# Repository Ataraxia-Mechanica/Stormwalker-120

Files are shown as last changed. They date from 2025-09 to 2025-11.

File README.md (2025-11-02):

# Stormwalker 120

Discord server:

https://discord.gg/DXYpTaRm

Stormwalker 120 is a Voron 0 sized (120mm^3 build size), ultra fast 3D printer designed for rapid prototyping. Press and forget, go through iterations in minutes!

in enclosure
nobackdrop-2k

# Project Currently Under Construction

Progress is currently made towards an assembly manual covering how to build and tune this printer, though it's possible to build it from just the BOM and referencing the 3D model in Blender.

If sourcing the components are hard or expensive, please wait for the kit of this printer as I am determined to make it a reality.

# Input Shaper Graph
x_new
y

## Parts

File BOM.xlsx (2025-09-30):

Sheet: Body
Category | Component/Item | Variant | Qty | Notes
Filament
Filament | ABS-GF | Fusrock NexABS-GF25 (Coextrusion 25% fill) 1kg | 1 | Qidi also sells repackaged fusrock. Non-coextruded ABS-GF would work.
Filament | PET-GF | FusRock FusForce PET-GF 500g | 1 | PET-CF would work. DO NOT BUY FROM POLYMAKER/BAMBU, FAILS DURING ANNEALING
Filament | MATTE PETG | 1kg | 1 | For Ebox, helper tools and fan duct.
Frame
Aluminum Extrusion | 3060 extrusion (3mm thickness) (Custom ordered) | 225mm | 2 | Commonly found 2mm thickness ones would work at reduced performance. Check custom ordered parts folder for holes/tapping
Aluminum Extrusion | 3060 extrusion (3mm thickness) (Custom ordered) | 200mm | 1
Aluminum Extrusion | 3060 extrusion (3mm thickness) (Custom ordered) | 140mm | 1
Steel Plate | Steel Plate (Custom ordered) | 304 stainless steel, 8mm thickness | 1 | 215mm*215mm*8mm
Frame Bracket | 90 Degree 3030 Corner Bracket |  | 2 | Optional. Check model for clearance. Some variants would limit max Z travel.
Rubber Feet | 40mm Screw Mount Round Large Rubber Feet | M6 hole | 4
Motion
Belt | Gates EPDM LL-2GT-9mm High Temperature Belt | 2.4mm closed loop belt | 1 | Uses ~800mm for Y axis and ~550mm for X.
Pulleys | Gates 2GT 20 tooth pulley | 8mm bore, 9mm wide | 4 | Use geniue Gates/Runice high matching pulleys. Do not cheap out. 9mm and 10mm wide pulleys are the same thing (11mm groove width).
Pulleys | Gates 2GT 20 tooth pulley | 5mm bore, 9mm wide | 2
Bearing | Bearing 625ZZ | ABEC7/P4 | 2 | ABEC 5/P5 min, ABEC7/P4 or better recommended.
Stepper Motor | Moons' NEMA17 2A | MS17HD6P420I-04 | 2
Stepper Motor | SUMTOR 1.3A NEMA17 8mm shaft | 42HS813A4D8 | 4
Stepper Motor | Integrated Lead Screw Stepper | Nema17 40mm TR8x1 | 2 | Commonly found TR8x2 would work, but 1mm thread pitch helps with layer stacking quality.
Heatsink | Heatsink | 30x40x5mm | 14 | 3 of each for X steppers, and 2 of each for Y steppers
Toolhead
Stepper Motor | Moon's Nema14 Pancake 10T | CSE14RA1L410A-01 | 1 | Must be 10T.
Extruder | K1 all metal extruder gear | Double bearing | 1 | Comes in pairs, only need one. Must be double bearing variant, see image on the right.
Extruder | K1 all metal reduction gear |  | 1
Hotend | TZ-E3 2.0 |  | 1
Hotend Extender | 35mm Super Extender (Custom ordered) |  | 1 | Check custom ordered parts folder. Might need to screw in a M6 screw for a few times to loosen it due to thin walls and bad manufacturing.
Belt Clip | X Axis Belt Clip (Custom ordered) |  | 2
Thermistor | Generic 3950 Thermistor | glass bead, 1.2mm diameter | 1
Heater | Ceramic Heater 7mm*35mm | 7~8Ω | 1
Bearing | Miniature Bearing MR63ZZ | ABEC7/P4 | 1 | ABEC7/P4 or better recommended. Replaces the low quality one from K1 reduction gear.
Bearing | Miniature Bearing 693ZZ | ABEC7/P4 | 1 | ABEC7/P4 or better recommended. Add to the front of the extruder gear for extra stability.
Bearing | U Groove Bearing U624ZZ | 1.5mm wide*0.5mm deep groove | 1
PTFE Tube | PTFE Tube | 1.8mm ID * 2.6mm OD | 1 | Smaller diameter tubes constrain the filament better.
Pin | Stainless Steel Pin | 3mm*14mm | 1
Pin | Stainless Steel Pin | 3mm*20mm | 1
Pin | Stainless Steel Pin | 4mm*10mm | 1
Hotend Cooling Fan | 3015 Fan | 24V 12000RPM | 1 | Higher the CFM the better. At least 5CFM.
Spring | Sherpa Mini Spring | 0.7mm Wire Width*5mm OD*15mm Length | 1
Bimetal Nozzle | Bimetal Volcano Nozzle |  | 1
Rail
Linear Rail | MGW15 | 200mm (Z1 preload) | 1 | Cheap ones work just as well.
Linear Rail | MGW9 | 240mm (Z1 preload), 2 carriages | 2
Linear Rail | Airtac LRW9L | LRW9L 1X174S12AH | 2 | Must be Airtac and no preload.
Bed
Carbon Fiber Bed | Carbon Fiber Sheet (Custom ordered) | 120*120mm (3K - 4mm Plain Matte) | 1 | Check custom ordered parts folder.
Heater | 1mm Aluminum PCB (Custom ordered) |  | 1
Thermister | Generic 3950 100K | Surface Mounted 0805 Size | 1
Magnetic Sheet | 2mm Magnetic Sheet | Extra strong, 120mm*120mm | 1 | Optional.
PEI Sheet | Voron 0 Textured PEI |  | 1 | Consider getting 2 of them to minimize downtime between prints.
Cooling
Cooling Fan | Delta 4056 Fan | GFC0412DS-SM06 | 3 | Weaker variants would work.
Misc.
Popcorn Salt | Popcorn Salt |  | 200g | Pack PET parts tightly in salt and air fry for 2 hours at 130-140C.
Glue | 425 Glue |  | 1 | Basically plastic-safe threadlocker. Apply on screws after installing. Warning: if accidentally went into screw socket, immediately insert screwdriver into socket and wait 30 seconds for it to dry to prevent gluing the socket shut.
Glue | 407 Glue |  | 1
RTV Silicone | RTV Silicone | Temp resistant to 300℃ | 1
Dish Soap | Dish Soap |  | 5mL | For making custom RTV silicone socks. Rinse the mold with dish soap water.
Lubrication Grease | Mobilux EP2 |  | 5mL | For lubricating linear rails.
Lubrication Grease | PTFE Grease |  | 5mL | For lubricating lead screws and extruder gears.
Thermal Paste | Thermal Paste | Temp resistant to 350℃ | 2mL | Paste eaters are the most oppressed group in society. Replaces the godawful GD900 that comes with TZE3.

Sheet: Ebox&Wiring
Category | Component/Item | Variant | Qty | Notes
Electronics
Power Supply | LRS-350-24 |  | 1
Power Supply | LRS-150-48 |  | 1
Board | Fly-C8 |  | 1
WiFi Dongle | WiFi Dongle | MT7601 | 1 | Fly-C8 doesn't support the addon WiFi module if you don't use the bloat filled system image. Flawless design.
SD Card | SD Card | 32GB | 1
Stepper Driver | Stepper Driver | TMC2209 | 2 | Z axis.
Stepper Driver | Stepper Driver | TMC2240 | 1 | E axis.
Stepper Driver | Stepper Driver | TMC5160 | 2
MOSFET Board | MOSFET Board | 10A peak | 1 | The board's default fan ports can't keep up with 2.8A server fans.
Breakout Board
Breakout Board | Microbreak board (Custom ordered) |  | 1 | Check custom ordered parts folder.
Wire Connector | Micro-Fit 3.0 Vertical Header, Dual Row | 430452412 (2x12) | 1
Wire Connector | Micro-Fit 3.0 Vertical Header, Dual Row | 430452012 (2x10) | 1
Wire Connector | JST XH Series Straight Through Hole PCB Header | 2 Pin | 12
Wire Connector | JST XH Series Straight Through Hole PCB Header | 4 Pin | 9
Screw Terminal Block | Screw Terminal Block | 2pin, 3.5mm pitch | 3 | Both top entry and side entry would work.
Harness
Crimp Terminal | Micro-Fit 3.0 Crimp Terminal, Female |  | 50 | Uses 43. Buy extra if not confident with wiring.
Wire | Insulated wire | 26AWG | 15m
Wire | Insulated wire | 20AWG | 15m
Wire Housing | Micro-Fit 3.0 Receptacle Housing, Dual Row | 430252400 (2x12) | 1 | Buy extra if not confident with wiring.
Wire Housing | Micro-Fit 3.0 Receptacle Housing, Dual Row | 430252000 (2x10) | 1
Wire Connector | JST XH Series Connector | 2 Pin | 12
Wire Connector | JST XH Series Connector | 4 Pin | 9
Wiring
Wire Connector | JST XH Series Connector | 2 Pin | 12
Wire Connector | JST XH Series Connector | 3 Pin | 4
Wire | Silicone wire | 26AWG | 5m | For wiring thermistors and endstops.
Wire | Silicone wire | 20AWG | 8m | For wiring heaters and fans.
Wire | Silicone wire | 16AWG, Black | 1m | Neutral/-
Wire | Silicone wire | 16AWG, Red | 1m | Live/24V
Wire | Silicone wire | 16AWG, Green+Yellow | 1m | GND
Wire | Silicone wire 4 Strand | 20AWG | 230mm | For bed heater and thermistor.
Wire Splicing Connector | Wago 221-413 |  | 4
Misc.
Endstops | D2F style microswitch | No lever | 4 | Use expensive ones for Z axis. Can use cheap ones for X and Y.
Wire Sleeve | Split Braided Sleeving | 6mm | 2m | 600mm for toolhead and 1.2m for harness.
Ebox Cooling Fan | Fan | 9225 | 2
Power Socket | AC-17 IEC320 C14 Electrical AC Power Socket | With top and bottom screw holes | 1

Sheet: Fasteners
Category | Component/Item | Variant | Qty | Notes
Screws (Body)
Screw | Self Tapping | M2x10 | 4 | For X and Y endstops.
Screw | BHCS | M2x35 | 2
Screw | BHCS | M3x6 | 4
Screw | BHCS | M3x10 | 4
Screw | BHCS | M3x14 | 5
Screw | BHCS | M3x20 | 4
Screw | BHCS | M6x12 | 12 | 4 extra for Y belt tensioner.
Screw | BHCS | M6x30 | 8
Screw | BHCS | M6x50 | 2
Screw | BHCS | M8x35 | 6
Screw | BHCS | M8x90 | 2
Screw | Small Head Screw | M3x16, head diameter 4.5mm | 2 | Oops. Doesn't have enough clearance for regular screws on the toolhead unless you switch to LDO pancake motor and lose torque.
Screw | Ultra Low Head Socket Cap | M4x14 | 4 | Lower than 1.2mm head height, so it can sink below the magnetic sheet.
Screw | SHCS | M1.6x12 TC4 | 4 | Must be in titanium TC4 for hotend double shear.
Screw | SHCS | M3x8 | 4
Screw | SHCS | M3x10 | 29
Screw | SHCS | M3x12 | 29
Screw | SHCS | M3x22 | 8
Screw | SHCS | M3x25 | 12
Screw | SHCS | M3x30 | 8
Screw | SHCS | M3x35 | 4
Screw | SHCS | M3x50 | 2
Screw | SHCS | M3x60 | 12
Screw | SHCS | M4x16 | 10
Screw | SHCS | M5x30 | 8
Screws (Ebox)
Screw | FHCS | M4x8 | 4
Screw | FHCS | M3x10 | 4
Screw | SHCS | M3x35 | 8
Screw | BHCS | M3x6 | 18
Nuts
Nut | M3 Nut |  | 2
Nut | M4 Nut |  | 10
Nut | M6 Nut |  | 12
Self-Clinching Nut | Self-Clinching Nut | CLS-M6-00 (304 stainless steel, thinnest variant) | 1 | For hotend double shear. Stainless steel ones are preferred due to low heat conduction.
T nut | 2020 M3 Nut |  | 32 | Due to the geometry of the 3.0mm 3060 extrusion, only 2020 nuts can fit in. Use NoDrop nuts provided to hold them in place during assembly. If using normal 3060 extrusion, get 3030 ones.
T nut | 2020 M5 Nut |  | 8
Threaded Heat Insert | M1.6 Threaded Heat Insert | M1.6x2.5x5 | 4 | Dimensions are in hole diameter x outer diameter x height. Some vendors use hole diameter x height x outer diameter, check before buying.
Threaded Heat Insert | M2 Threaded Heat Insert | M2x3x4 | 2
Threaded Heat Insert | M3 Threaded Heat Insert | M3x5x4 ("Voron Style") | 44
Threaded Heat Insert | M3 Threaded Heat Insert | M3x5x10 | 12
Threaded Heat Insert | M6 Threaded Heat Insert | M6x8x10 | 6 | 4 of them are for belt tensioner.
Shim
Shim | M3 Shim | M3x16x1, stainless steel | 2 | 10mm~16mm diameter ones would work. Grind the top surface on the extrusion away, and put the sharp side of the shim towards the extrusion to ground the frame.

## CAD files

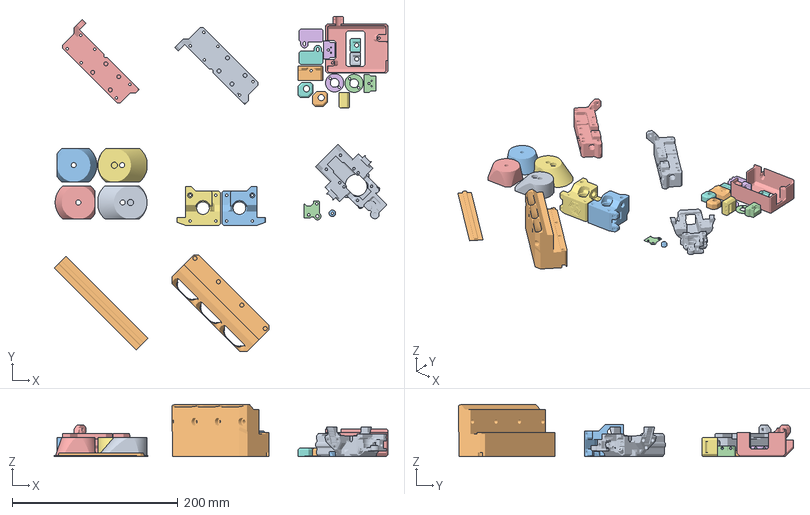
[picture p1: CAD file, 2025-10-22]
3mf/ABS-GF.3mf
402.6 x 404.4 x 62.8 mm
Longboi_toolhead.stl
Aux_Cooling.stl
TZE3_plug.stl
Front_cover.stl
PCB_cover.stl
PCB_spacer_A.stl
Slim_Feet_Support_Back.stl x 2
PCB_spacer_B.stl
Toolhead_Strain_Relief.stl
Slim_Feet_Support_Front.stl x 2
Nut_Shim.stl x 2
Motor_Mount.stl
Feet_Holder.stl x 2
Long_Z.stl x 2
Motor_Mount_Left.stl
Z_Endstop.stl x 2
Y_endstop.stl
NoDrop-2020_chopped.stl x 2
3030_cover.stl

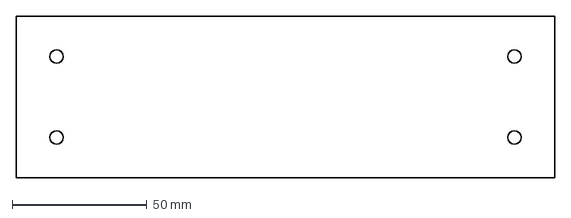
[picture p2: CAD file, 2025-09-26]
custom ordered parts/3060 extrusions/Extrusion Holes.dxf
200.0 x 60.0 mm

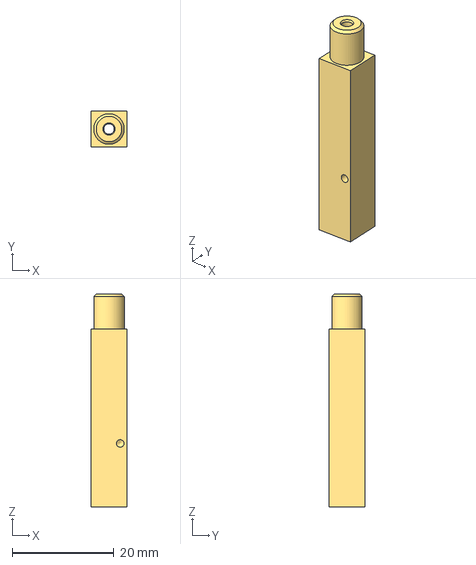
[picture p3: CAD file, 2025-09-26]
custom ordered parts/35mm super extender/Super Extender 35mm.step
7.00 x 7.00 x 41.9 mm

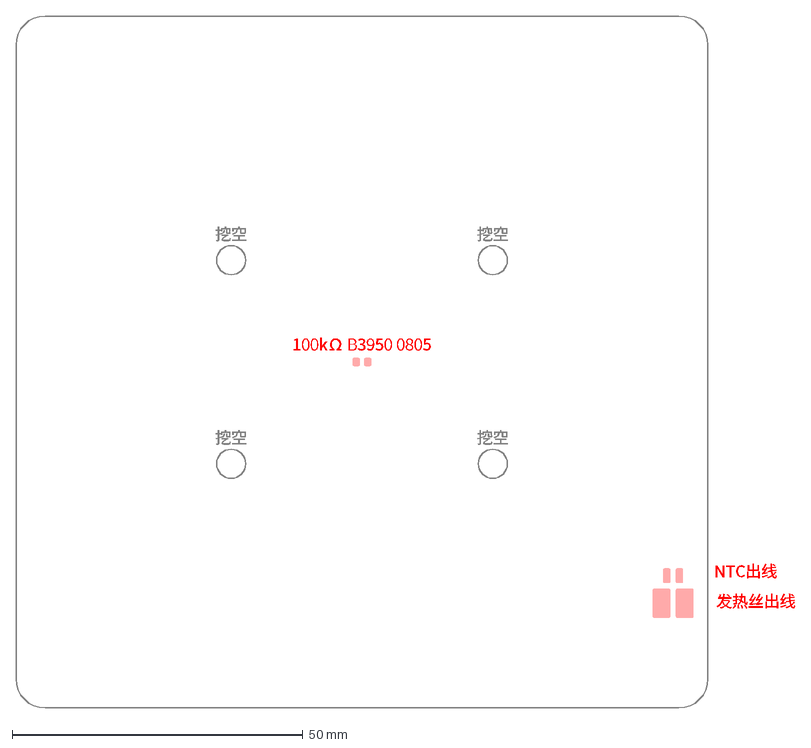
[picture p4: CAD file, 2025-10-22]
custom ordered parts/custom_PI_heater/24V 125W.dxf
100kΩ B3950 0805
NTC出线
发热丝出线
挖空

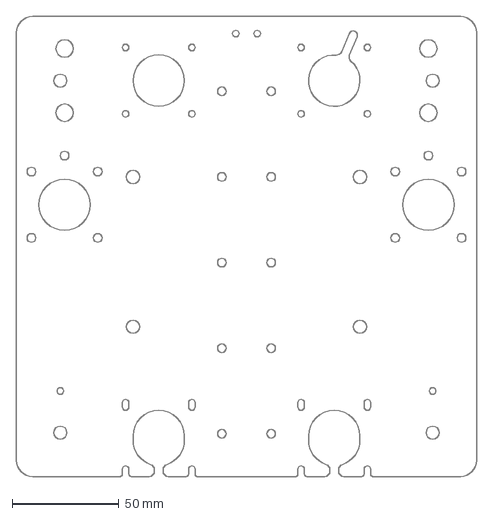
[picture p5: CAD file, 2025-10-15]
custom ordered parts/Steel bottom plate 8mm.dxf
215.0 x 215.0 mm

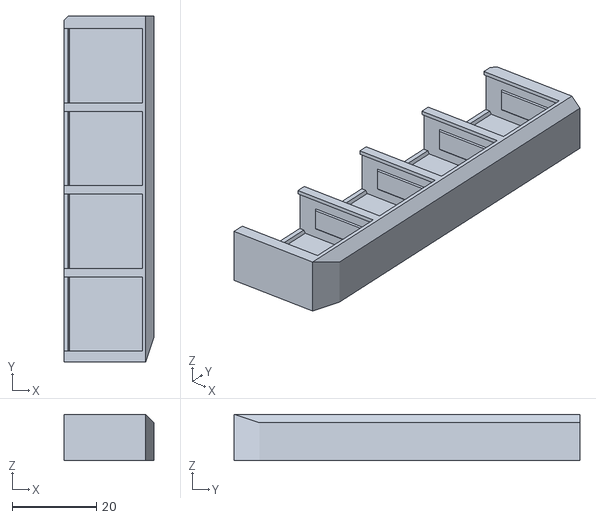
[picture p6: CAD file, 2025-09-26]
micro ebox/stl/4x_Wago_221.stl
21.4 x 82.0 x 11.0

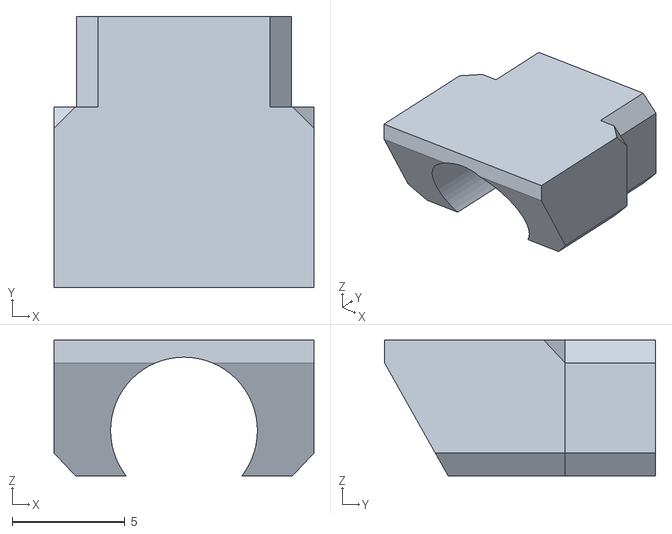
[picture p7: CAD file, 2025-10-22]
stl/Bed_Strain_Relief.stl
11.5 x 12.0 x 6.00

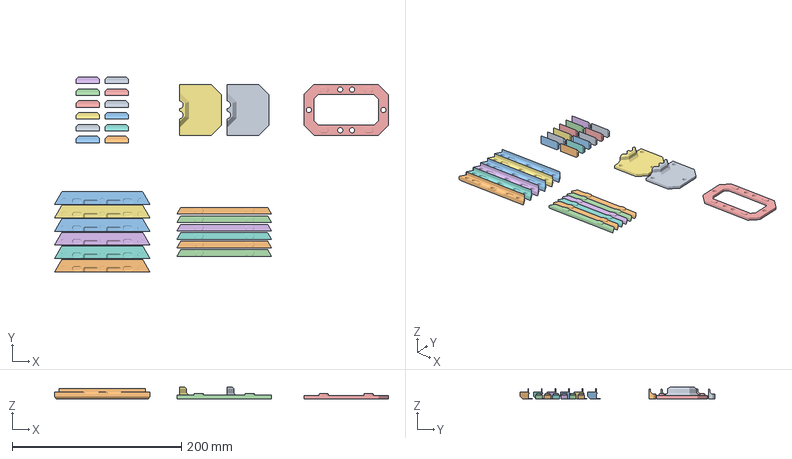
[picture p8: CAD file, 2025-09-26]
storm-in-a-box/3mf/Magnetic_Attacher.3mf
394.4 x 230.5 x 14.0 mm
Magnetic_Attacher.stl x 12
Panel_Attacher.stl x 6
Panel_Support.stl x 6
Ring.stl
Cover.stl x 2

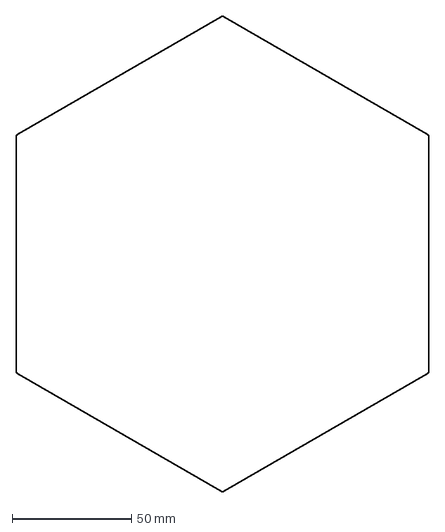
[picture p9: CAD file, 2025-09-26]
storm-in-a-box/Acrylic (5mm).dxf
173.2 x 199.8 mm

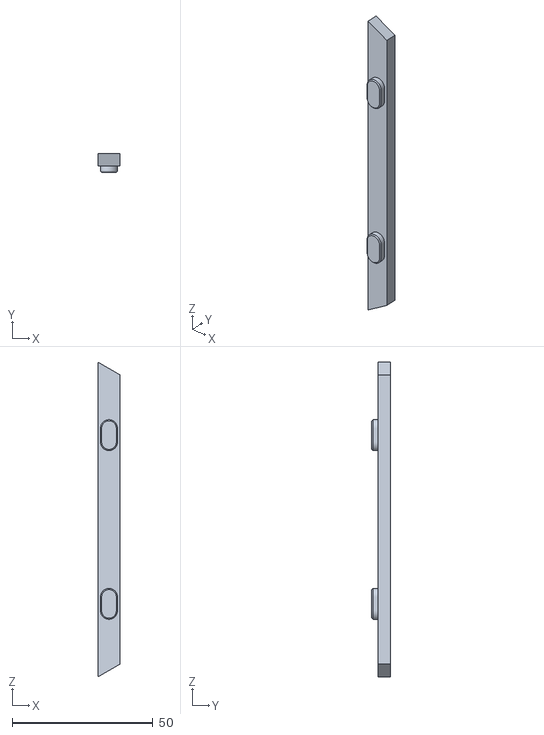
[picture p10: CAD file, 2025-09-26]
storm-in-a-box/stl/Panel_Attacher.stl
8.00 x 6.60 x 112.0

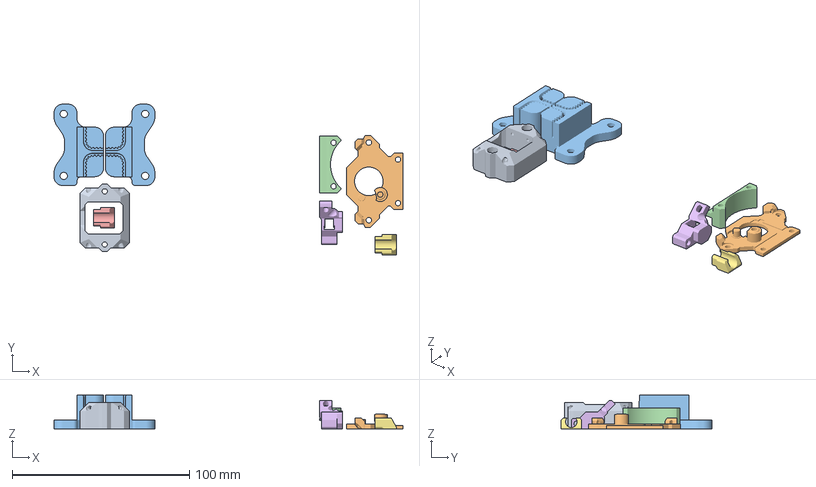
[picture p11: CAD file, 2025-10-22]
3mf/PET.3mf
197.1 x 85.1 x 19.0 mm
Crossover_Toolhead_PET.stl
Extruder_back_panel.stl
Assembly
Extruder_motor_support.stl
Bed_Strain_Relief.stl x 2
Idler_arm.stl

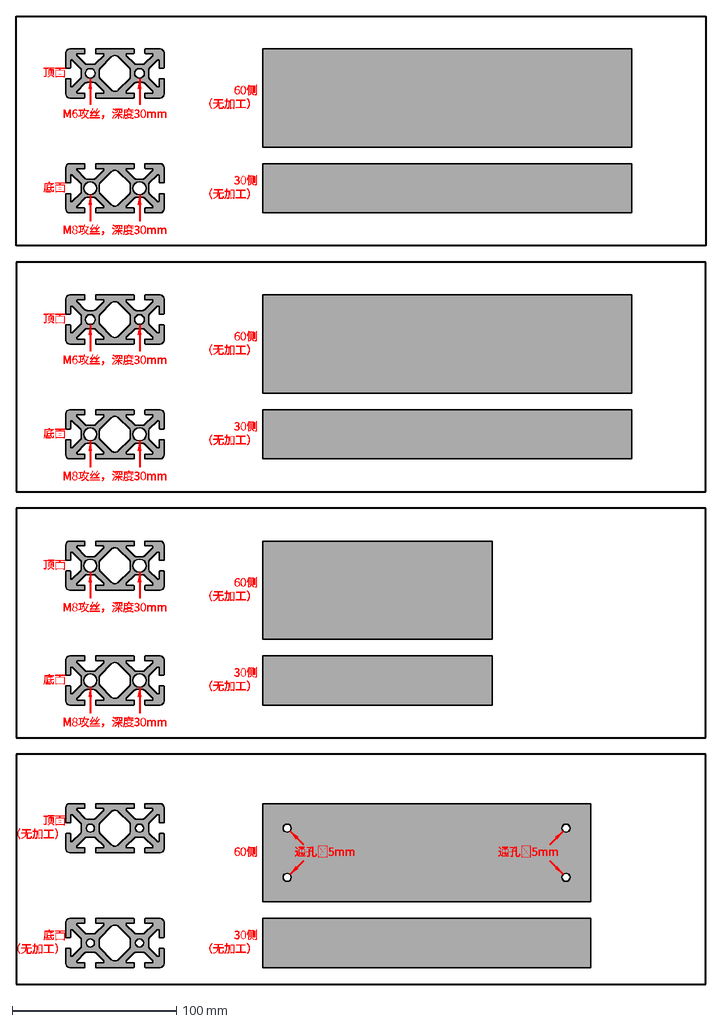
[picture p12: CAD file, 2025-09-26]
custom ordered parts/3060 extrusions/Extrusions.dxf
顶面
底面
60侧 （无加工）
30侧 （无加工）
顶面 （无加工）
底面 （无加工）
60侧
M8攻丝，深度30mm
M6攻丝，深度30mm

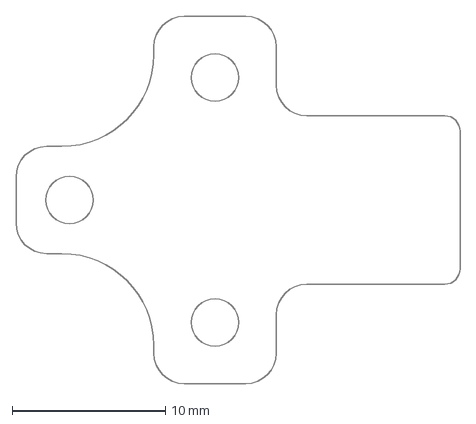
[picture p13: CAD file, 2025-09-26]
custom ordered parts/6061 X clip 3mm.dxf
29.0 x 24.0 mm

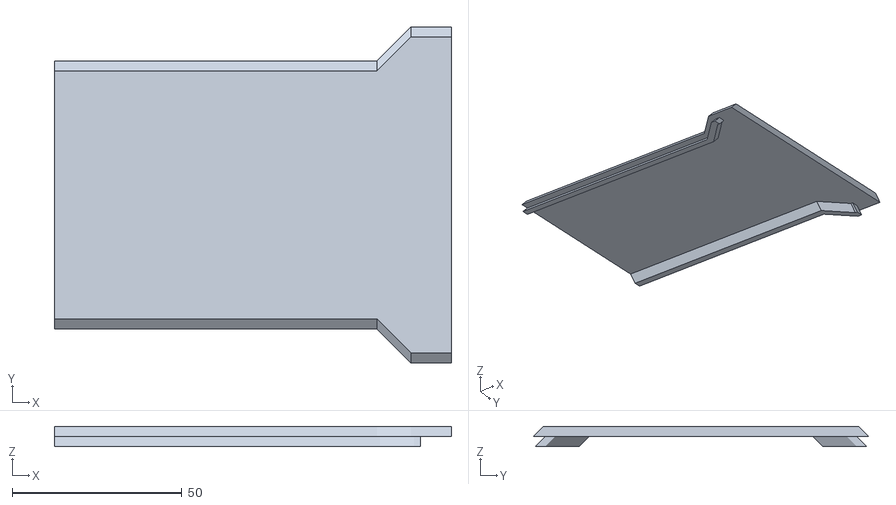
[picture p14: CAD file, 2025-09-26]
micro ebox/stl/Shell3.stl
117.0 x 99.0 x 6.00

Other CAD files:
stl/Extruder_back_panel.stl
storm-in-a-box/3mf/Light.3mf
storm-in-a-box/stl/Light2.stl
3mf/Sock.3mf
3mf/Extra_Ballast.3mf
3mf/PETG.3mf
Jigs & Tools.blend
custom ordered parts/35mm super extender/Super Extender 35mm.dxf
custom ordered parts/CF bed 4mm.dxf
micro ebox/stl/Back.stl
micro ebox/stl/Front.stl
micro ebox/stl/Shell1.stl
micro ebox/stl/Shell2.stl
micro ebox/stl/Shell4.stl
micro ebox/stl/Shell5.stl
micro ebox/stl/Shell6.stl
micro ebox/stl/Wedge.stl
micro ebox/stl/Wire_out.stl
micro ebox/stl/ebox.3mf
stl/3030_cover.stl
stl/Bed_Support.stl
stl/Crossover_Toolhead.stl
stl/Crossover_Toolhead_ABS.stl
stl/Crossover_Toolhead_PET.stl
stl/Extra_Ballast.stl
stl/Extruder_motor_support.stl
stl/Extruder_motor_support_COMPROMISE.stl
stl/Feet_Holder.stl
stl/Front_cover.stl
stl/Idler_arm.stl
stl/Long_Z.stl
stl/Motor_Mount.stl
stl/Motor_Mount_Left.stl
stl/NoDrop-2020.stl
stl/NoDrop-2020_chopped.stl
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

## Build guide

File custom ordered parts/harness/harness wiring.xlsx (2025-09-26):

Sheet: 24pin
name | type | wire gauge | pin
EM1 | XHP4 | 22 | 14 |  | motor slot 8
 |  |  | 13
 |  |  | 2
 |  |  | 1
XR0 | SCREW TERMINAL | 22 | 3 | + | PD13
 |  |  | 4 | -
XR1 | SCREW TERMINAL | 22 | 5 | + | PD14
 |  |  | 6 | -
XEND1 | XHP3 | / | / |  | PD10
 |  | / | /
 |  | 26 | 7
XM | SCREW TERMINAL | 22 | 8 | A+ | TMC5160X | cooling fan: PA1
 |  |  | 9 | A-
 |  |  | 10 | B+
 |  |  | 11 | B-
AUXF | SOLDERING | 22 | 12 | - | PD12 (through mosfet) | mosfet fan: PA2
 |  |  | 24 | +
HEF | XHP2 | 26 | 15 |  | PC7
 |  |  | 16
XTH0 | XHP2 | 26 | 17 |  | PC4
 |  |  | 18
XTH1 | XHP2 | 26 | 19 |  | PC3
 |  |  | 20
GND | SCREW TERMINAL | 22 | 21 | GND
FANPWM | XHP2 | / | / |  | PC6
 |  | 26 | 23

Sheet: 20pin
name | type | wire gauge | pin
YR1 | SCREW TERMINAL | 22 | 1 | + | PB0
 |  |  | 2 | -
YTH1 | XHP2 | 26 | 3 |  | PC2
 |  |  | 4
ZM0 | XHP4 | 26 | 15 |  | motor slot 6
 |  |  | 16
 |  |  | 6
 |  |  | 5
YM | SCREW TERMINAL | 22 | 7 | A+ | TMC5160Y | cooling fan: PA0
 |  |  | 8 | A-
 |  |  | 9 | B+
 |  |  | 10 | B-
ZEND0 | XHP3 | / | / |  | PD8
 |  | / | /
 |  | 26 | 11
ZEND1 | XHP3 | / | / |  | PD9
 |  | / | /
 |  | 26 | 12
YEND1 | XHP3 | / | / |  | PD11
 |  | 26 | 14
 |  | 26 | 13
ZM1 | XHP4 | 26 | 20 |  | motor slot 7
 |  |  | 19
 |  |  | 18
 |  |  | 17

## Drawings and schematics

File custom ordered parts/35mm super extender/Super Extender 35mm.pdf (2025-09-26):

A

## 2 THRU

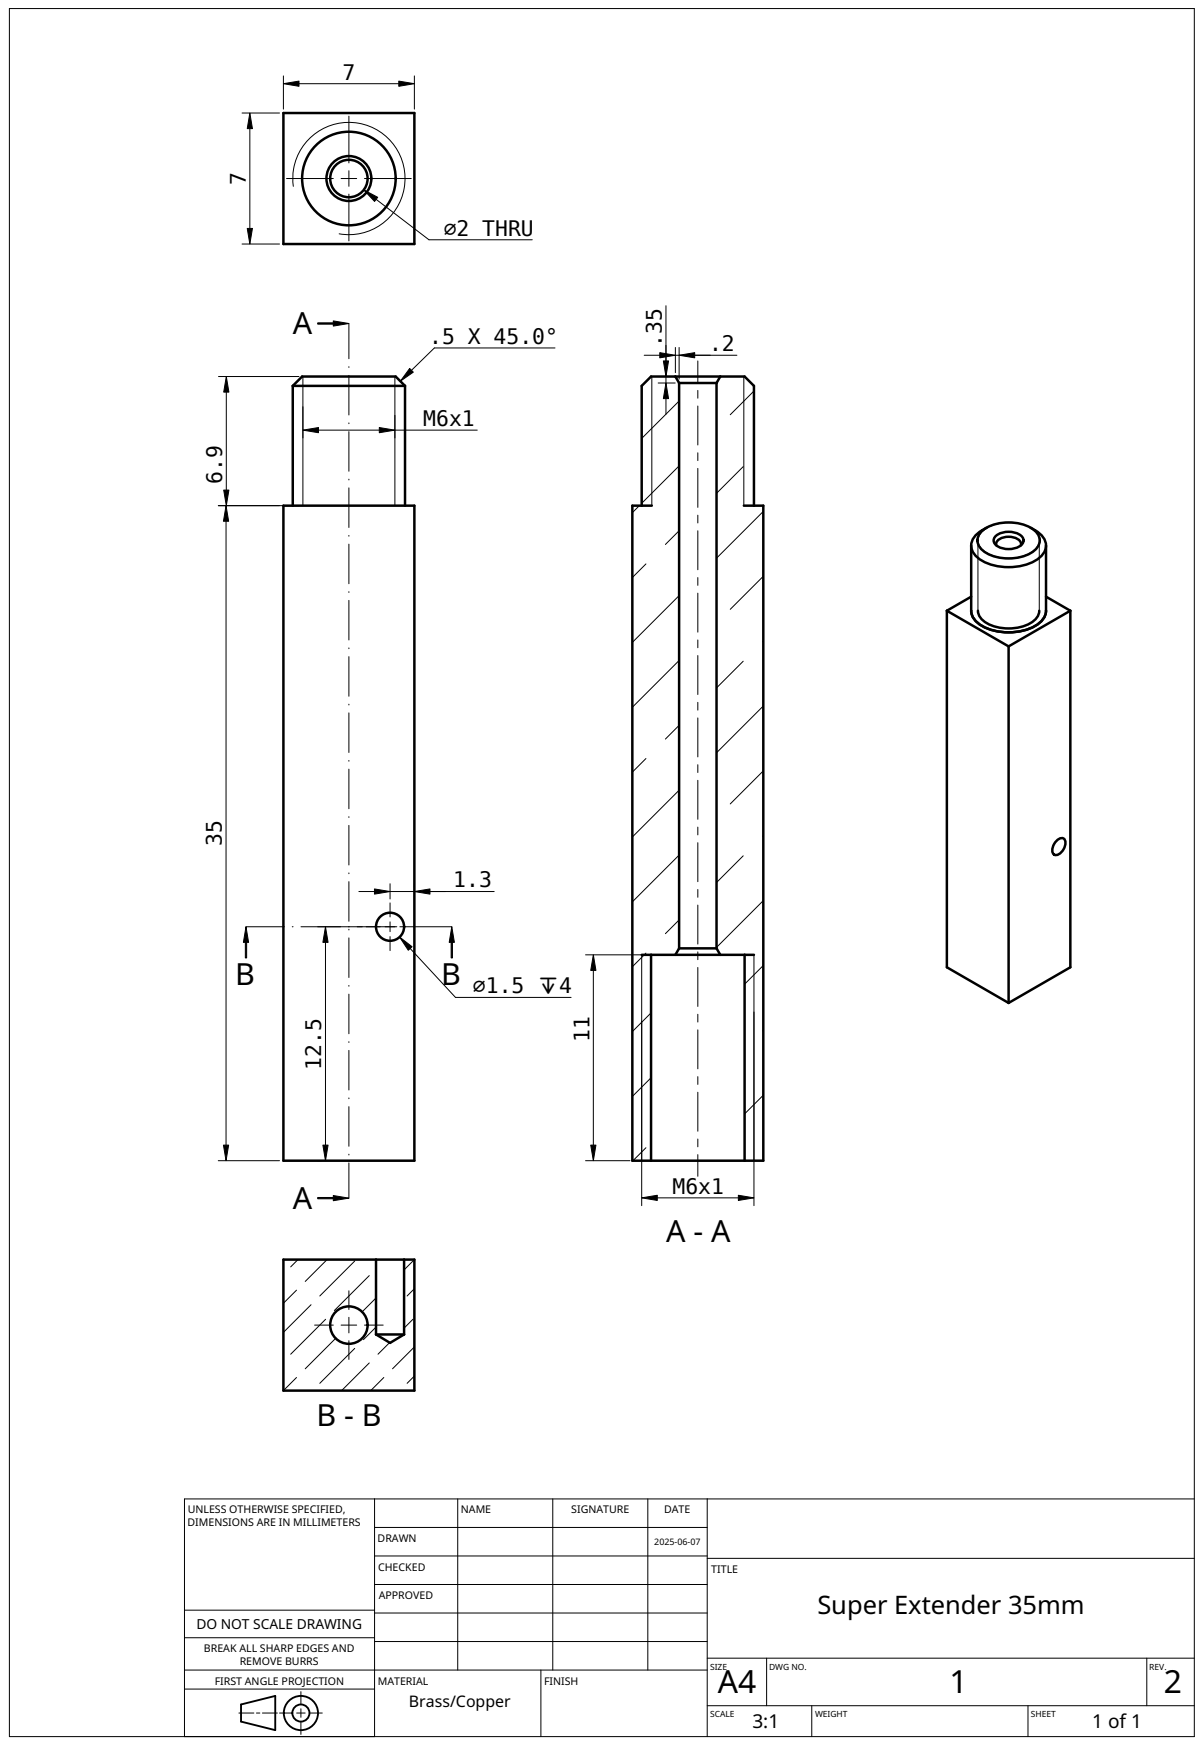
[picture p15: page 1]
MATERIAL Brass/Copper; FINISH

UNLESS OTHERWISE SPECIFIED, DIMENSIONS ARE IN MILLIMETERS | | NAME | SIGNATURE | DATE

DRAWN | | | 2025-06-07

CHECKED | | | | TITLE Super Extender 35mm

APPROVED

DO NOT SCALE DRAWING

BREAK ALL SHARP EDGES AND

REMOVE BURRS
FIRST ANGLE PROJECTION

SIZE A4 | DWG NO. 1 | REV. 2

SCALE 3:1 | WEIGHT | SHEET 1 of 1

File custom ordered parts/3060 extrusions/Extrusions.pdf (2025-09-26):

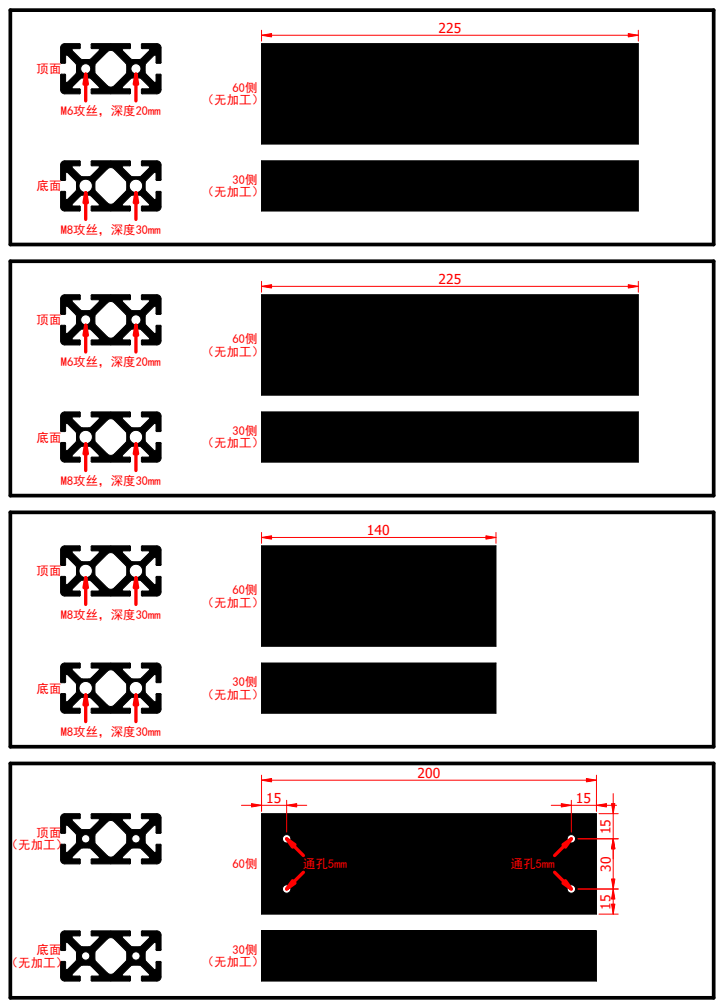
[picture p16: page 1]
60侧 （无加工）; 30侧 （无加工）; 顶面 （无加工）; 底面 （无加工）

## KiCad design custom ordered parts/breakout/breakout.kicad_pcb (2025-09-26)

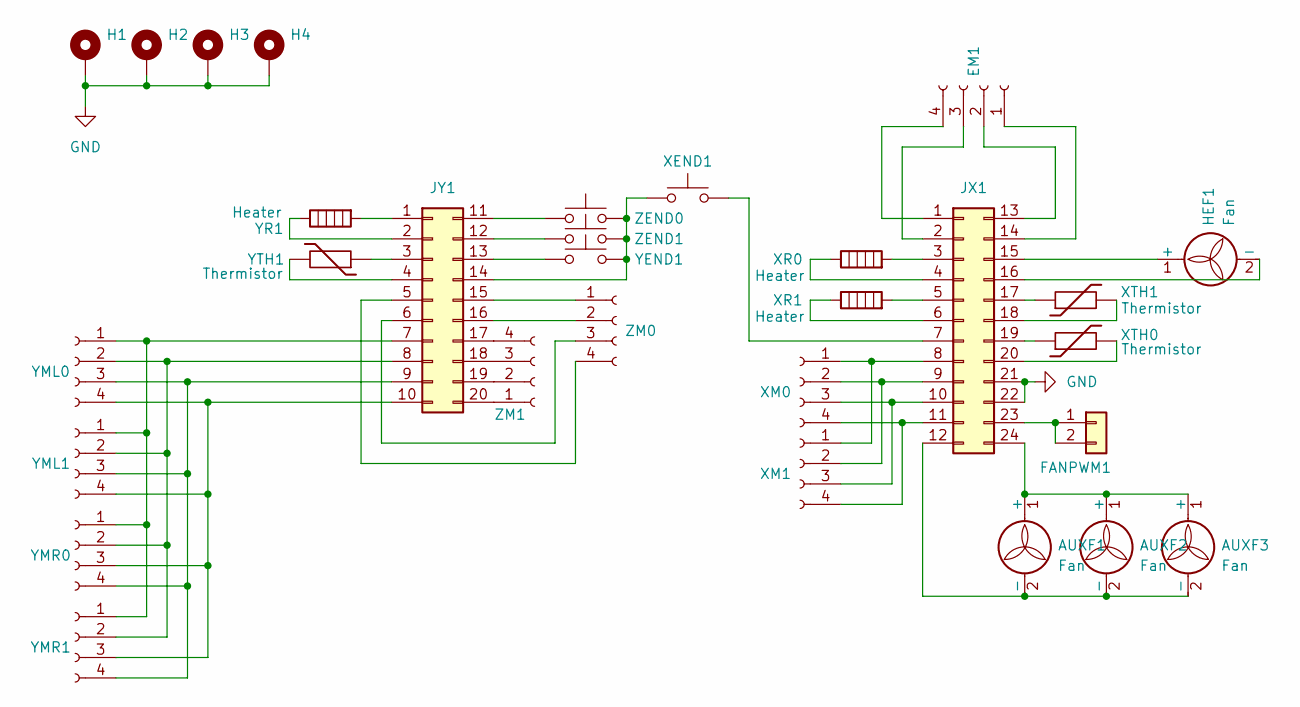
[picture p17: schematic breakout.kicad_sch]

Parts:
AUXF1, AUXF2, AUXF3: Fan; JST_XH_B2B-XH-A_1x02_P2.50mm_Vertical
EM1: Conn_01x04_Socket; JST_XH_B4B-XH-A_1x04_P2.50mm_Vertical
FANPWM1: Conn_01x02; JST_XH_B2B-XH-A_1x02_P2.50mm_Vertical
H1, H2, H3, H4: MountingHole_Pad; MountingHole_3.2mm_M3_DIN965_Pad_TopBottom
HEF1: Fan; JST_XH_B2B-XH-A_1x02_P2.50mm_Vertical
JX1: Conn_02x12_Top_Bottom; Molex_Micro-Fit_3.0_43045-2412_2x12_P3.00mm_Vertical
JY1: Conn_02x10_Top_Bottom; Molex_Micro-Fit_3.0_43045-2012_2x10_P3.00mm_Vertical
XEND1: SW_Push; JST_XH_B2B-XH-A_1x02_P2.50mm_Vertical
XM0, XM1: Conn_01x04_Socket; JST_XH_B4B-XH-A_1x04_P2.50mm_Vertical
XR0, XR1: Heater; TerminalBlock_4Ucon_1x02_P3.50mm_Horizontal
XTH0, XTH1: Thermistor; JST_XH_B2B-XH-A_1x02_P2.50mm_Vertical
YEND1: SW_Push; JST_XH_B2B-XH-A_1x02_P2.50mm_Vertical
YML0, YML1: Conn_01x04_Socket; JST_XH_B4B-XH-A_1x04_P2.50mm_Vertical
YMR0, YMR1: Conn_01x04_Socket; JST_XH_B4B-XH-A_1x04_P2.50mm_Vertical
YR1: Heater; TerminalBlock_4Ucon_1x02_P3.50mm_Horizontal
YTH1: Thermistor; JST_XH_B2B-XH-A_1x02_P2.50mm_Vertical
ZEND0, ZEND1: SW_Push; JST_XH_B2B-XH-A_1x02_P2.50mm_Vertical
ZM0, ZM1: Conn_01x04_Socket; JST_XH_B4B-XH-A_1x04_P2.50mm_Vertical

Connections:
GND: H1.1, H2.1, H3.1, H4.1, JX1.21, JX1.22
unnamed 1: AUXF1.1 (+), AUXF2.1 (+), AUXF3.1 (+), JX1.24; also elsewhere on the board
unnamed 2: AUXF1.2 (-), AUXF2.2 (-), AUXF3.2 (-), JX1.12; also elsewhere on the board
unnamed: EM1.1, JX1.14
unnamed: EM1.2, JX1.13
unnamed: EM1.3, JX1.2
unnamed: EM1.4, JX1.1
unnamed: FANPWM1.1, FANPWM1.2, JX1.23
unnamed: HEF1.1 (+), JX1.15
unnamed: HEF1.2 (-), JX1.16
unnamed: JX1.3, XR0.2
unnamed: JX1.4, XR0.1
unnamed: JX1.5, XR1.2
unnamed: JX1.6, XR1.1
unnamed: JX1.7, XEND1.2
unnamed: JX1.8, XM0.1, XM1.1
unnamed: JX1.9, XM0.2, XM1.2
unnamed: JX1.10, XM0.3, XM1.3
unnamed: JX1.11, XM0.4, XM1.4
unnamed: JX1.17, XTH1.1
unnamed: JX1.18, XTH1.2
unnamed: JX1.19, XTH0.1
unnamed: JX1.20, XTH0.2
unnamed: JY1.1, YR1.2
unnamed: JY1.2, YR1.1
unnamed: JY1.3, YTH1.1
unnamed: JY1.4, YTH1.2
unnamed: JY1.5, ZM0.4
unnamed: JY1.6, ZM0.3
unnamed: JY1.7, YML0.1, YML1.1, YMR0.1, YMR1.1
unnamed: JY1.8, YML0.2, YML1.2, YMR0.2, YMR1.2
unnamed: JY1.9, YML0.3, YML1.3, YMR0.4, YMR1.4
unnamed: JY1.10, YML0.4, YML1.4, YMR0.3, YMR1.3
unnamed: JY1.11, ZEND0.2
unnamed: JY1.12, ZEND1.2
unnamed: JY1.13, YEND1.1
unnamed: JY1.14, XEND1.1, YEND1.2, ZEND0.1, ZEND1.1
unnamed: JY1.15, ZM0.1
unnamed: JY1.16, ZM0.2
unnamed: JY1.17, ZM1.4
unnamed: JY1.18, ZM1.3
unnamed: JY1.19, ZM1.2
unnamed: JY1.20, ZM1.1

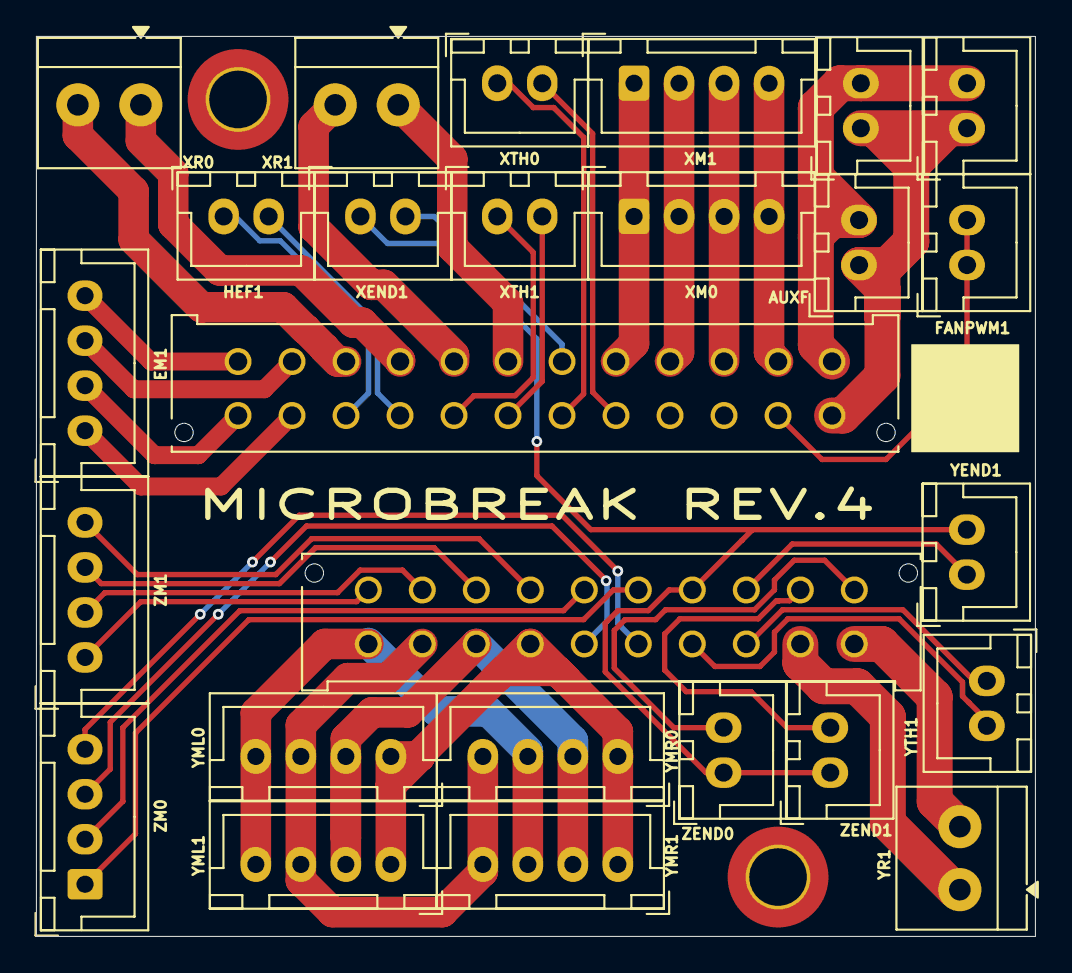
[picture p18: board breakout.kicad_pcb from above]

Board: 2 copper layers, 55.5 x 50.0 mm, 28 parts (0 on the bottom side), 43 nets.

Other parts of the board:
AUXF: Fan; JST_XH_B2B-XH-A_1x02_P2.50mm_Vertical

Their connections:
unnamed 1: AUXF.1 (+); also elsewhere on the board
unnamed 2: AUXF.2 (-); also elsewhere on the board

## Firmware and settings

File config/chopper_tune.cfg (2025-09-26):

[gcode_macro CHOPPER_TUNE]
description: Vibrations tests to calculate lowest magnitude drivers registers v1.2      ; https://github.com/MRX8024/chopper-resonance-tuner
variable_debug: False                                                                   ; Enable debug output
variable_inset: 10                                                                      ; Offset from axis limits (mm), to determine work area limits
variable_current_change_step: 25                                                        ; Set run_current change step
variable_measure_time: 400                                                              ; Set measure time (msec)
variable_required_rpm: [37.5, 150, 1.5]                                                 ; Set range, step of motor rpm in find vibr mode
variable_delay: 300                                                                     ; Set delay between measurements (msec) in find vibr mode
variable_fclk: 12
gcode:
    {% set current_min = params.CURRENT_MIN_MA|default('default')|string|lower %}
    {% set current_max = params.CURRENT_MAX_MA|default('default')|string|lower %}
    {% set tbl_min = params.TBL_MIN|default(0)|int %}
    {% set tbl_max = params.TBL_MAX|default(3)|int %}
    {% set toff_min = params.TOFF_MIN|default(1)|int %}
    {% set toff_max = params.TOFF_MAX|default(8)|int %}
    {% set hstrt_hend_max = params.HSTRT_HEND_MAX|default(16)|int %}
    {% set hstrt_min = params.HSTRT_MIN|default(0)|int %}
    {% set hstrt_max = params.HSTRT_MAX|default(7)|int %}
    {% set hend_min = params.HEND_MIN|default(2)|int %}
    {% set hend_max = params.HEND_MAX|default(15)|int %}
    {% set tpfd_min = params.TPFD_MIN|default(-1)|int %}
    {% set tpfd_max = params.TPFD_MAX|default(-1)|int %}
    {% set min_speed = params.MIN_SPEED|default('default')|string|lower %}
    {% set max_speed = params.MAX_SPEED|default('default')|string|lower %}
    {% set speed_change_step = params.SPEED_CHANGE_STEP|default('default')|string|lower %}
    {% set iterations = params.ITERATIONS|default(1)|int %}
    {% set travel_distance = params.TRAVEL_DISTANCE|default('default')|string|lower %}
    {% set accel_chip = params.ACCELEROMETER|default('default')|string|lower %}
    {% set find_vibr = params.FIND_VIBRATIONS|default('False')|string|lower %}
    {% set axis = params.AXIS|default('X')|string|lower %}
    {% set run_plotter = params.RUN_PLOTTER|default('True')|string|lower %}

    _detect_driver stepper={axis}
    _chop_workflow axis={axis} {rawparams}

[gcode_shell_command chop_tune]
command: ~/chopper-resonance-tuner/chopper_plot.sh
timeout: 9999.0
verbose: True

[gcode_macro _detect_driver]
description: Find which driver is used in configuration
variable_drivers: '2130', '2208', '2209', '2660', '2240', '5160' ; Drivers supported by Klipper
variable_driver: 0
variable_resistor: 0
gcode:
    {% set stepper = 'stepper_' + params.STEPPER|string|lower %} ; Import default stepper for search its driver
    {% for driver in drivers %}
        {% if 'run_current' in printer.configfile.config['tmc' + driver + ' ' + stepper] %}
            {action_respond_info('Selected tmc%s for %s' % (driver, stepper))}
            SET_GCODE_VARIABLE MACRO=_detect_driver VARIABLE=driver VALUE={driver}
            {% if driver != '2240' %}
                {% set resistor = printer.configfile.settings['tmc' + driver + ' ' + stepper].sense_resistor %}
            {% else %}
                {% set resistor = printer.configfile.settings['tmc' + driver + ' ' + stepper].rref %}
            {% endif %}
                SET_GCODE_VARIABLE MACRO=_detect_driver VARIABLE=resistor VALUE={resistor}
        {% endif %}
    {% endfor %}

[gcode_macro _chop_apply_regs]
variable_registers: 'tbl', 'toff', 'hend', 'hstrt', 'tpfd', 'curr'
variable_amount: 0
variable_tbl:   -1
variable_toff:  -1
variable_hend:  -1
variable_hstrt: -1
variable_tpfd:  -1
variable_curr:  -1
gcode:
    {% if printer['gcode_macro _chop_apply_regs'][params.FIELD]|int != params.VALUE|int %}
        {% for stepper in params.STEPPERS.split('-') %}
            {% if printer['gcode_macro CHOPPER_TUNE'].debug %}
                M118 Setting {params.FIELD|string|lower} from {
                 printer['gcode_macro _chop_apply_regs'][params.FIELD]|int} to {params.VALUE|int} on {stepper}
            {% endif %}
            {% if params.FIELD|lower != 'curr' %}
                SET_TMC_FIELD STEPPER={stepper} FIELD={params.FIELD} VALUE={params.VALUE|int}
            {% else %}
                SET_TMC_CURRENT STEPPER={stepper} CURRENT={params.VALUE|int / 1000}
            {% endif %}
            {% for count in range(1, amount + 1) %}
                {% if printer['gcode_macro CHOPPER_TUNE'].debug %}
                    M118 Setting {params.FIELD|string|lower} from {
                     printer['gcode_macro _chop_apply_regs'][params.FIELD]|int} to {
                      params.VALUE|int} on {stepper|string + count|string}
                {% endif %}
                {% if params.FIELD|lower != 'curr' %}
                    SET_TMC_FIELD STEPPER={stepper|string + count|string} FIELD={params.FIELD} VALUE={params.VALUE|int}
                {% else %}
                    SET_TMC_CURRENT STEPPER={stepper} CURRENT={params.VALUE|int / 1000}
                {% endif %}
            {% endfor %}
        {% endfor %}
        SET_GCODE_VARIABLE MACRO=_chop_apply_regs VARIABLE={params.FIELD|string|lower} VALUE={params.VALUE|int}
    {% endif %}

[gcode_macro _chop_workflow]
description: Calculate process of CHOPPER_TUNE macro
gcode:
    {% set axis = params.AXIS|default('X')|string|lower %}
    {% set driver = printer['gcode_macro _detect_driver'].driver|string|lower %}        ; Import default driver from _detect_driver
    {% set sense_resistor = printer['gcode_macro _detect_driver'].resistor %}           ; Import sense_resistor from _detect_driver
    {% set current_min = params.CURRENT_MIN_MA|default('default')|string|lower %}       ; Import rawparams from CHOPPER_TUNE params
    {% set current_max = params.CURRENT_MAX_MA|default('default')|string|lower %}
    {% set current_change_step = printer['gcode_macro CHOPPER_TUNE'].current_change_step %}
    {% set tbl_min = params.TBL_MIN|default(0)|int %}
    {% set tbl_max = params.TBL_MAX|default(3)|int %}
    {% set toff_min = params.TOFF_MIN|default(1)|int %}
    {% set toff_max = params.TOFF_MAX|default(8)|int %}
    {% set hstrt_hend_max = params.HSTRT_HEND_MAX|default(16)|int %}
    {% set hstrt_min = params.HSTRT_MIN|default(0)|int %}
    {% set hstrt_max = params.HSTRT_MAX|default(7)|int %}
    {% set hend_min = params.HEND_MIN|default(2)|int %}
    {% set hend_max = params.HEND_MAX|default(15)|int %}
    {% set tpfd_min = params.TPFD_MIN|default(-1)|int %}
    {% set tpfd_max = params.TPFD_MAX|default(-1)|int %}
    {% set min_speed = params.MIN_SPEED|default('default')|string|lower %}
    {% set max_speed = params.MAX_SPEED|default('default')|string|lower %}
    {% set speed_change_step = params.SPEED_CHANGE_STEP|default('default')|string|lower %}
    {% set required_rpm = printer['gcode_macro CHOPPER_TUNE'].required_rpm %}
    {% set iterations = params.ITERATIONS|default(1)|int %}
    {% set travel_distance = params.TRAVEL_DISTANCE|default('default')|string|lower %}
    {% set accel_chip = params.ACCELEROMETER|default('default')|string|lower %}
    {% set find_vibr = params.FIND_VIBRATIONS|default('False')|string|lower %}
    {% set run_plotter = params.RUN_PLOTTER|default('True')|string|lower %}
    {% set inset = printer['gcode_macro CHOPPER_TUNE'].inset %}
    {% set config = printer.configfile.config %}
    {% set settings = printer.configfile.settings %}
    {% set measure_time = printer['gcode_macro CHOPPER_TUNE'].measure_time / 1000|float %}
    {% set delay = printer['gcode_macro CHOPPER_TUNE'].delay|int %}
    {% set fclk = printer['gcode_macro CHOPPER_TUNE'].fclk|int %}
    {% set kinematics = config.printer.kinematics|string %}

    ; Select main and secondary axis / stepper, their requirements
    {% if axis in ['x', 'y', 'z'] %}
        {% if kinematics == 'corexy' %}
            {% if axis in ['x', 'y'] %}
                {% if axis == 'x' %}
                    {% set axes = ['x', 'y'] %}
                {% elif axis == 'y' %}
                    {% set axes = ['y', 'x'] %}
                {% endif %}
                {% set steppers = ['stepper_x', 'stepper_y'] %}
            {% elif axis == 'z' %}
                {% set axes = ['z', 'x'] %}
                {% set steppers = ['stepper_z'] %}
            {% endif %}
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

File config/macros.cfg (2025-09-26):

#selective motor powering off
# [gcode_macro M84]
# rename_existing:M84.1
# gcode:
#   {% if 'X' in params or 'Y' in params or 'Z' in params or 'E' in params %}
#   {% if 'X' in params %}
#       SET_STEPPER_ENABLE STEPPER=stepper_x enable=0
#       SET_STEPPER_ENABLE STEPPER=stepper_x1 enable=0
#   {% endif %}
#   {% if 'Y' in params %}
#       SET_STEPPER_ENABLE STEPPER=stepper_y enable=0
#   {% endif %}
#   {% if 'Z' in params %}
#       SET_STEPPER_ENABLE STEPPER=stepper_z enable=0
#       SET_STEPPER_ENABLE STEPPER=stepper_z1 enable=0
#   {% endif %}
#   {% if 'E' in params %}
#       SET_STEPPER_ENABLE STEPPER=extruder enable=0
#   {% endif %}
#   {% else %}
#       SET_STEPPER_ENABLE STEPPER=stepper_x enable=0
#       SET_STEPPER_ENABLE STEPPER=stepper_x1 enable=0
#       SET_STEPPER_ENABLE STEPPER=stepper_y enable=0
#       SET_STEPPER_ENABLE STEPPER=stepper_z enable=0
#       SET_STEPPER_ENABLE STEPPER=stepper_z1 enable=0
#       SET_STEPPER_ENABLE STEPPER=extruder enable=0
#   {% endif %}

#from LH stinger
[gcode_macro AWD_SYNC]
description: Remember to move the bed to the center and loosen left stepper's pulley grub screws (when syncing X) or 3 of the steppers' pulley grub screws (when syncing Y).  
gcode:
    {% set iterations = params.ITERATIONS|default(4)|int %}
    {% set p_time = params.PAUSE_TIME|default(0)|int %}
  
    {% for i in range(iterations) %}
      SET_KINEMATIC_POSITION X=60 Y=60 Z=20 
      G91
      ### Moving to full step motor position
      G1 X0.1 Y0.1
      
      G1 X0.02 Y0.02
      G1 X-0.02 Y-0.02
      {% if i < (iterations-1) %}
        M84
      {% endif %}
      G4 P500
      {% if i == 1 %}
        G4 P{1000*p_time}
      {% endif %}
    {% endfor %}
    G90
    # Done

#control both
[gcode_macro M104]
rename_existing: M104.1
gcode:
  {% set s = params.S|default(0)|float %}

  SET_HEATER_TEMPERATURE HEATER=extruder     TARGET={s+10}
  SET_HEATER_TEMPERATURE HEATER=lower_heater TARGET={s}


[gcode_macro M109]
rename_existing: M109.1
gcode:
  {% set s = params.S|default(0)|float %}
  
  M104 S{s}
  {% if s != 0 %}
    # TEMPERATURE_WAIT SENSOR=extruder     MINIMUM={s-2} MAXIMUM={s+2}
    TEMPERATURE_WAIT SENSOR=extruder     MINIMUM={s+8} MAXIMUM={s+12}
    TEMPERATURE_WAIT SENSOR="heater_generic lower_heater" MINIMUM={s-2} MAXIMUM={s+2} ;why?
  {% endif %}

[gcode_macro M190]
rename_existing: M190.1
gcode:
  {% set s = params.S|default(0)|float %}
  
  M140 S{s}
  {% if s != 0 %}
    TEMPERATURE_WAIT SENSOR=heater_bed MINIMUM={s-0.5} MAXIMUM={s+2}
  {% endif %}


[gcode_macro PRINT_START]
gcode:
  {% set extruder = params.EXTRUDER|default(220)|float %}
  {% set bed = params.BED|default(60)|float %}
  {% set accel = params.ACCEL|default(80000)|int %}

  RESPOND msg="Travel acceleration is {accel}"
  {% if accel <= 50000 %}
    RESPOND msg="Entering low current mode"
    SET_TMC_CURRENT STEPPER=stepper_x CURRENT=2.4
    SET_TMC_CURRENT STEPPER=stepper_y CURRENT=3.0
  {% elif accel <= 100000 %}
    RESPOND msg="Entering normal current mode"
    SET_TMC_CURRENT STEPPER=stepper_x CURRENT=3.2
    SET_TMC_CURRENT STEPPER=stepper_y CURRENT=4.0
  {% else %}
    RESPOND msg="Entering racing mode. Do not run this inside an enclosure!"
    SET_TMC_CURRENT STEPPER=stepper_x CURRENT=3.4
    SET_TMC_CURRENT STEPPER=stepper_y CURRENT=4.8
  {% endif %}

  M140 S{bed}
  G28
  TEMPERATURE_WAIT SENSOR=heater_bed MINIMUM={bed-15} MAXIMUM={bed+2}
  G90                       ;absolute positioning
  M83                       ;absolute extrusion
  M107                      ;fan off
  SET_VELOCITY_LIMIT ACCEL=10000
  G1 Z5 F300                ;lift up
  G92 E0                    ;reset extrusion
  G1 X90 Y0.5 F6000           ;to front
  G1 Z0.5 F300              ;lower
  M104 S{extruder}
  M109 S{extruder}
  M190 S{bed}

  G1 X30 E60 F240           ;extrude to the left
  G1 E-0.4 F3000 
  G1 Z2 F300                ;lift further up
  G1 X2 F30000              ;fast travel to break stringing
  G1 Z0                     ;drop down

  SET_VELOCITY_LIMIT ACCEL=50000
  G17                       ;arc at xy plane to remove string
  G2 I0 J1 Z0.2 E0.2 F24000
  G92 E0                    ;reset extrusion

[gcode_macro PRINT_END]
gcode:
  M400                      ;wait for buffer to clear
  {% set max_x = printer.configfile.config["stepper_x"]["position_max"]|float %}
  {% set max_y = printer.configfile.config["stepper_y"]["position_max"]|float %}
  {% set max_z = printer.configfile.config["stepper_z"]["position_max"]|float %}

  ;Check end position to determine safe direction to arc
  {% if printer.toolhead.position.x < (max_x  / 2) %}
      {% set i_safe = 1.0 %}
  {% else %}
      {% set i_safe = -1.0 %}
  {% endif %}

  {% if printer.toolhead.position.y < (max_y / 2) %}
      {% set j_safe = 1.0 %}
  {% else %}
      {% set j_safe = -1.0 %}
  {% endif %}

  ;edge condition: if in a corner, no direction is safe to spin
  {% set nospin = (printer.toolhead.position.x < 1 or printer.toolhead.position.x > (max_x - 1)) and (printer.toolhead.position.y < 1 or printer.toolhead.position.y > (max_y - 1)) %}

  {% if printer.toolhead.position.z < (max_z - 0.4) %}
      {% set z_safe = printer.toolhead.position.z + 0.4 %}
  {% else %}
      {% set z_safe = max_z %}
  {% endif %}

  {% if (z_safe + 5) < (max_z - 3) %}
      {% set final_park_z = z_safe + 5 %}
  {% else %}
      {% set final_park_z = max_z - 3 %}
  {% endif %}

  G90                                       ;absolute positioning
  G92 E0                                    ;zero the extruder
  G1 E-2 F4200                              ;fast retract filament

  SET_VELOCITY_LIMIT ACCEL=30000
  {% if nospin == true %}
    G1 Z{z_safe}
  {% else %}
    G17                                     ;arc at xy plane
    G2 I{i_safe} J{j_safe} Z{z_safe} F24000 ;spin to reduce filament stringing
  {% endif %}

  SET_VELOCITY_LIMIT ACCEL=10000
  TURN_OFF_HEATERS
  M107                                      ;turn off fan
  G1 X{max_x / 2} Y{max_y - 2} Z{final_park_z} F3600        ;park nozzle at center back
  G1 E-15.0 F600
  G92 E0
  FORCE_MOVE STEPPER=stepper_z1 DISTANCE={0 - printer.save_variables.variables.zr_offset} VELOCITY=2
  M400
  G4 P2000
  M84 ;turn off motors

[gcode_macro CANCEL_PRINT]
description: Cancel the actual running print
rename_existing: CANCEL_PRINT_BASE
gcode:
  CANCEL_PRINT_BASE
  PRINT_END

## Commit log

2025-09-26 Stormwalker 1.0 prerelease
    [4x_Wago_221.stl, 6061 X clip 3mm.dxf, ABS-GF.3mf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]
2025-09-26 Reinforce extruder idler
    Broke again :(
    [ABS-GF.3mf, Idler_arm.stl]
2025-09-29 Oops, forgot the nozzle
    [BOM.xlsx]
2025-09-29 Ignore more kicad temp files
2025-09-29 Use SMT thermistor on the bed which is more reliable and cheaper
    [BOM.xlsx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]
2025-09-29 Dish soap
    [BOM.xlsx]
2025-09-29 Bed wiring update
    Strain Relief and bigger holes on the breakout pcb cover
    [ABS-GF.3mf, Bed_Strain_Relief.stl, PCB_cover.stl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]
2025-09-29 Fix Z column geometry
    [Long_Z.stl]
2025-09-30 Forgot 4 Screws, literally unbuildable
    [BOM.xlsx]
2025-10-05 Add dust cover for X axis extrusion
    [3030_cover.stl, ABS-GF.3mf]
2025-10-11 Strengthened the extruder further
    Now handles filled filaments in a heated chamber well
    [ABS-GF.3mf, Crossover_Toolhead_ABS.stl, Front_cover.stl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]
2025-10-15 Switch to PET for some parts for heat resistance
    [ABS-GF.3mf, Extruder_back_panel.stl, Idler_arm.stl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]
2025-10-15 Tilt the grub screw access hole to the right
    [Steel bottom plate 8mm.dxf]
2025-10-22 Fix small error in strain relief
    [ABS-GF.3mf, Bed_Strain_Relief.stl, PET.3mf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]
2025-10-22 Polymide bed heater
    [24V 125W.dxf]
